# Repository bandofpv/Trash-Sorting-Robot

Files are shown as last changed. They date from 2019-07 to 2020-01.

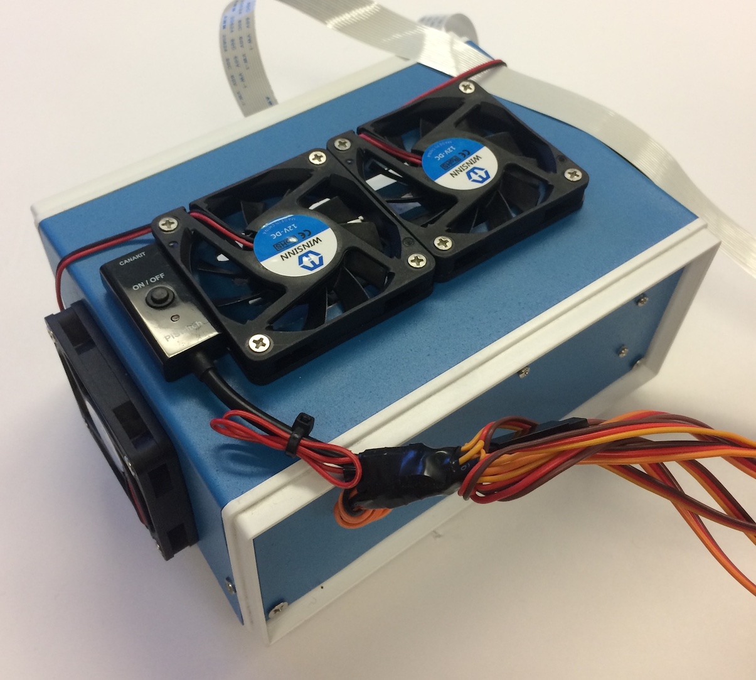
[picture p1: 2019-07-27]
Images/project-box-out.JPG

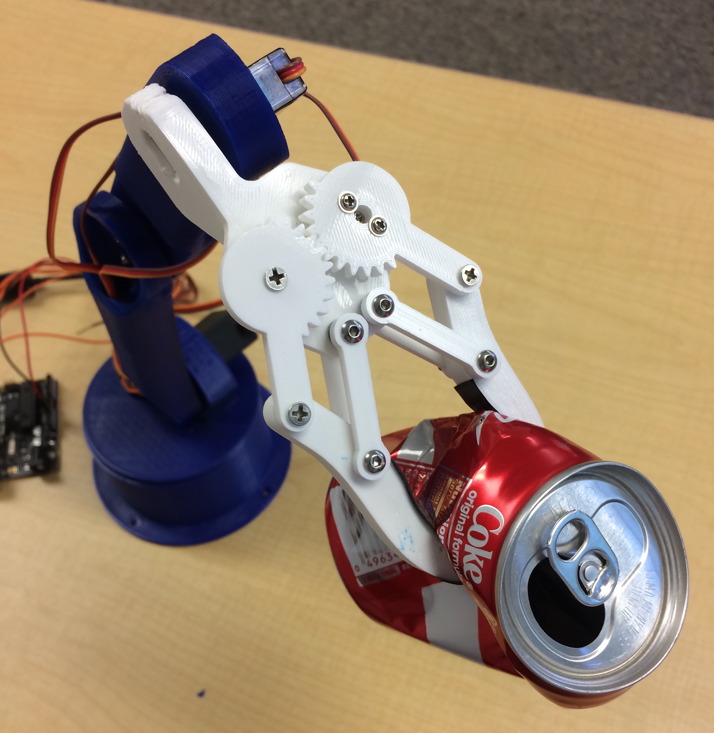
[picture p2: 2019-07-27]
Images/robotic-claw-can.JPG

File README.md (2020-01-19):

# Trash_Sorting_Robot

## Helpful Resources:

* [Recycle Image Set](https://github.com/garythung/trashnet)
* [How to Train Tensorflow Object Detection Model on Windows 10](https://github.com/EdjeElectronics/TensorFlow-Object-Detection-API-Tutorial-Train-Multiple-Objects-Windows-10)
* [How to Train Tensorflow Lite Object Detection Model in Cloud TPUs](https://medium.com/tensorflow/training-and-serving-a-realtime-mobile-object-detector-in-30-minutes-with-cloud-tpus-b78971cf1193)
* [How to Build and Install Tensorflow From Source on Windows 10](https://medium.com/@amsokol.com/how-to-build-and-install-tensorflow-gpu-cpu-for-windows-from-source-code-using-bazel-d047d9342b44)
* [Object Detection with Google Coral USB Accelerator](https://www.pyimagesearch.com/2019/05/13/object-detection-and-image-classification-with-google-coral-usb-accelerator/)
* [USB-to-Serial Communication with Raspberry Pi and Arduino](https://www.sunfounder.com/blog/rpi-ard/)
* [3D Printed Robotic Arm](https://howtomechatronics.com/tutorials/arduino/diy-arduino-robot-arm-with-smartphone-control/)

## Repository Contents:

### [Arduino](https://github.com/bandofpv/Trash_Sorting_Robot/tree/master/Arduino) - files used for Arduino to control robotic arm:
* [basicMovement](https://github.com/bandofpv/Trash_Sorting_Robot/tree/master/Arduino/basicMovement) - .ino file to perform basic movement with robotic arm
* [roboticArm](https://github.com/bandofpv/Trash_Sorting_Robot/tree/master/Arduino/roboticArm) - .ino file to control robotic arm to pick up and drop off a piece of recycling detected from the Raspberry Pi

### [Documentation](https://github.com/bandofpv/Trash_Sorting_Robot/tree/master/Documentation) - files documenting my build process:
* [Bill_of_Materials.pdf](https://github.com/bandofpv/Trash_Sorting_Robot/blob/master/Documentation/Bill_of_Materials.pdf) - .pdf file including all my parts used in my project 
* [Notebook.pdf](https://github.com/bandofpv/Trash_Sorting_Robot/blob/master/Documentation/Notebook.pdf) - .pdf file including my notebook that I used when building my robot

### [Images](https://github.com/bandofpv/Trash_Sorting_Robot/tree/master/Images) - images of my project

### [RPI](https://github.com/bandofpv/Trash_Sorting_Robot/tree/master/RPI) - files used for Raspberry Pi to perform object detection:
* [recycle_ssd_mobilenet_v2_quantized_300x300_coco_2019_01_03](https://github.com/bandofpv/Trash_Sorting_Robot/tree/master/RPI/recycle_ssd_mobilenet_v2_quantized_300x300_coco_2019_01_03) - .tflite and .txt files of the trained recycle model and lables to perform object detection
* [recycle_detection.py](https://github.com/bandofpv/Trash_Sorting_Robot/blob/master/RPI/recycle_detection.py) - python code used to perform object detection and communicate with Arduino

### [Tensorflow](https://github.com/bandofpv/Trash_Sorting_Robot/tree/master/Tensorflow) - files used for training model:
* [CSV](https://github.com/bandofpv/Trash_Sorting_Robot/tree/master/Tensorflow/CSV) - .csv files of both the train and test image set
* [Images](https://github.com/bandofpv/Trash_Sorting_Robot/tree/master/Tensorflow/Images) - .jpg images of recycling materials and .xml files of the annotated images
* [SaveModel](https://github.com/bandofpv/Trash_Sorting_Robot/tree/master/Tensorflow/SaveModel) - frozen graph of trained model
* [TFLite](https://github.com/bandofpv/Trash_Sorting_Robot/tree/master/Tensorflow/TFLite) - .tflite file of trained model and .tflite file of compiled model for Google Coral USB Accelerator
* [TFRecord](https://github.com/bandofpv/Trash_Sorting_Robot/tree/master/Tensorflow/TFRecord) - .record files of both the train and test images set used for training
* [ssd_mobilenet_v2_quantized_300x300_coco_2019_01_03](https://github.com/bandofpv/Trash_Sorting_Robot/tree/master/Tensorflow/ssd_mobilenet_v2_quantized_300x300_coco_2019_01_03) - .config, .ckpt, and .pb files of the quantized model used for transfer learning
* [labelmap.pbtxt](https://github.com/bandofpv/Trash_Sorting_Robot/blob/master/Tensorflow/labelmap.pbtxt) - label map used for training

## Tutorial:

[Hackser.io Tutorial](https://www.hackster.io/bandofpv/recycle-sorting-robot-with-google-coral-b52a92)

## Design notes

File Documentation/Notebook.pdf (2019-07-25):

Important Links:

Waste sorting Medium:
https://towardsdatascience.com/how-to-build-an-image-classifier-for-waste-sorting-6d11d3c9c47 8 (https://towardsdatascience.com/how-to-build-an-image-classifier-for-waste-sorting-6d11d3c9c478)

An Edge TPU Demo Medium:
https://blog.ml6.eu/our-edge-tpu-demo-project-cbc9bea5a355?gi=7440a077a13c

Installing Tensorflow on windows Medium: https://medium.com/@amsokol.com/how-to-build-and-install-tensorflow-gpu-cpu-for-windows-fro m-source-code-using-bazel-d047d9342b44 (https://medium.com/@amsokol.com/how-to-build-and-install-tensorflow-gpu-cpu-for-windows-from-source-code-using-bazel-d047d9342b44)

Training model in 30 minutes Medium: https://medium.com/tensorflow/training-and-serving-a-realtime-mobile-object-detector-in-30-min utes-with-cloud-tpus-b78971cf1193 (https://medium.com/tensorflow/training-and-serving-a-realtime-mobile-object-detector-in-30-minutes-with-cloud-tpus-b78971cf1193)

Object Detection with Edge TPU Pyimagesearch: https://www.pyimagesearch.com/2019/05/13/object-detection-and-image-classification-with-google-coral-usb-accelerator/ (https://www.pyimagesearch.com/2019/05/13/object-detection-and-image-classification-with-google-coral-usb-accelerator/)

EdjeElectronics training model GitHub: https://github.com/EdjeElectronics/TensorFlow-Object-Detection-API-Tutorial-Train-Multiple-Obj ects-Windows-10 (https://github.com/EdjeElectronics/TensorFlow-Object-Detection-API-Tutorial-Train-Multiple-Objects-Windows-10)

Trashnet GitHub: https://github.com/garythung/trashnet

Communication between Raspberry Pi and Arduino via USB-to-Serial: https://www.sunfounder.com/blog/rpi-ard/

3D printed robotic arm:
https://howtomechatronics.com/tutorials/arduino/diy-arduino-robot-arm-with-smartphone-control/

June 10, 2019:

Goals: Get started labeling data & setup RPI.

What I did & learned: I got halfway with labeling my 2.5K+ images for object detection. I made the bordering boxes to big so I had to fix all of them. RIP. I got to boot up my RPI. I got to check my inventory. I learned a little about how to set up my RPI to work with my edge TPU accelerator. I learned that I took an L and deleted my trained model so I have to retrain it again.

I also learned that my laptops GPU is too old and I can’t make use of it in the tensorflow-gpu version. Maybe try to borrow someone else's?

Any code & documentation: Github of labeled images → https://github.com/bandofpv/Trash_Sorting_Robot/tree/61fb91e893919938b6e709a3e1639e927 30c2b46 (https://github.com/bandofpv/Trash_Sorting_Robot/tree/61fb91e893919938b6e709a3e1639e92730c2b46)

I githubbed my model but realized it was the wrong one and realized I deleted the right one. RIP.

Plan for tomorrow: Try to finish labeling images. Setup RPI to work with edge TPU accelerator. Hope I can set up my training environment with tensorflow v1.9.

June 11, 2019:

Goals: Work on labeling. Finish installing TPU stuff.

What I did & learned: I labeled more images. I attempted to ssh to my RPI but was unsuccessful. I tried setting up my edge TPU for the RPI but that was too much work for the day. I also finished setting up my training environment on my laptop.

Any code & documentation: Github of labeled images → https://github.com/bandofpv/Trash_Sorting_Robot/tree/e6b9e248af5a54a2eadbdeffdf42c4b608 3c089b (https://github.com/bandofpv/Trash_Sorting_Robot/tree/e6b9e248af5a54a2eadbdeffdf42c4b6083c089b)

Plan for tomorrow: Try to finish labeling and try to start training.

June 12, 2019:

Goals: Continue labeling. Try to get the real-time object tracking working with the edge TPU accelerator and RPI camera.

What I did & learned: I learned how to use google’s edge TPU classification engine and use the RPI camera to actually classify images as either the 1,000 different objects that are in the
COCO dataset. I also got to use the OpenCV library to get boxes around the object that the pre-trained model recognizes using the classification engine.

Any code & documentation: Github of labeled images → https://github.com/bandofpv/Trash_Sorting_Robot/tree/77f7b33f8d09e02bd1dfe609c44aa23b97 848fdc (https://github.com/bandofpv/Trash_Sorting_Robot/tree/77f7b33f8d09e02bd1dfe609c44aa23b97848fdc)

Plan for tomorrow: Finish labeling images. Try to start training. Maybe start programming Arduino. Work on documentation.

June 13, 2019:

Goals: Finish labeling. Get ready for training → convert XML to CSV to TFRecord.

What I did & learned: I learned how to convert my XML files to CSV and then to TFRecord files. I also learned how to configure the pipeline.config file used to my training. I learned how to delete a docker image and container.

Any code & documentation: Github of labeled images → https://github.com/bandofpv/Trash_Sorting_Robot/tree/8abc70e8a31fdf7ffc08f747d077cbad0e4 5af50 (https://github.com/bandofpv/Trash_Sorting_Robot/tree/8abc70e8a31fdf7ffc08f747d077cbad0e45af50)

Github of training files → https://github.com/bandofpv/train_files/tree/6059fe5c8c78cdadbbaaf28bb0fb8572eddbdcc0

Plan for tomorrow: Start the training and work on my robotic arm.

June 14, 2019:

Goals: Start the training

What I did & learned: I learned how to train my model locally. Realized that it takes forever to train so I’m going to train on the cloud using google's cloud TPUs. I also learned that of all the waste that we produce, 75% is recyclable, yet only 30% is actually recycled. This is because of the contamination rates in the recycling centers. Human sorting adds a huge amount of error in sorting through trash/recycle.

Any code & documentation: Don’t have any code yet because my model is still training. After training in the cloud instead of locally.

Plan for tomorrow: Try to finish up training and start converting it to .tflite and compile it for the edge tpu.

June 17, 2019:

Goals: Learn to control a servo with Arduino and communicate the RPI with the Arduino.

What I did & learned: I learned how to communicate the Arduino using serial. I can make the RPI control the Arduino and the other way around. For my project, I need the RPI to control the Arduino robotic arm. I also learned about inverse kinematics where I can possibly use the robotic arm and move it in a 3D plane based on coordinates. It would be really cool to have the robotic arm move to a certain coordinate based on where the piece of recycling is located at. I also learned how to better use the edge TPU classification functions to identify different objects. I got my code to say if it recognizes a certain object. This is great to recognize where to place the piece of recycling. So if it’s made out of metal, then it would place the object somewhere different then if the object is made of paper.

Any code & documentation: I didn’t have enough time to create a GitHub repository for my code but I will tomorrow.

Plan for tomorrow: Start making my robotic arm hopefully.

Documentation for the first milestone:

Today I completed my first milestone which was to train an object detection model to run on the Coral Edge TPU. In my project, I trained an object detection model to distinguish between different types of recycling.

The first step in completing my first milestone was to install the Coral Edge TPU Python API on to the Raspberry Pi (RPI) in order to use my Coral USB Accelerator. The Coral Accelerator is a TPU or a tensor processing unit that you can connect to any device through a USB (universal serial bus). TPUs are processors designed specifically for machine learning purposes and thus a lot faster and more power efficient when running ML (machine learning) compared to using the RPI’s CPU. That’s why it’s called an accelerator because it accelerates the ML processing. It also includes the word “Edge” meaning all the ML processing is done locally or on the device instead of in the cloud. Using the cloud, you will need good network speed and have to pay a fee in order to use it. Using the cloud for ML is basically using
someone else's powerful TPU, CPU, or GPU to process your ML data and receiving output data via the internet. The benefits of using the Edge TPU is that you don’t need access to the internet making it a lot more versatile option. I still want to sort through recycling even if I don’t have internet access! The Edge TPU is not powerful as the cloud solution but is suitable for my project due to the small amount of data I will be using.

After getting my RPI and Coral USB Accelerator to run a real-time object detection program using a pre-trained model, I immediately noticed how much faster the object detection was. When I tested the same model using only the RPI CPU I observed an average fps (frames per second) of 0.90. With the Coral USB Accelerator, I received an average fps of 10.40. That’s more than 11 times faster! It can process at higher rates.

There is a feature during the installation of the Coral TPU API to run the accelerator at a frequency twice the speed than the default frequency. However, there was a warning that it would get really hot and could cause burns. So I didn’t select this feature due to lack of cooling in my system. This being said, I could easily attach a small fan to cool the USB accelerator and get an fps twice as fast.

The Edge TPU also works best using USB 3 with it’s “host computer” or my RPI. Unfortunately, the RPI 3 Model B+ only has USB 2 capability, not taking full advantage of the Edge TPU’s USB 3. USB 2 transfers data at a slower rate than USB 3. This means if the RPI had USB 3 capability, I can get a faster fps due to the faster rate of data flow. Recently in June, RPI just released the RPI 4 Model B. It not only has a better CPU and RAM but also comes with USB 3 capability. Unfortunately, the Raspbian OS version is built around Python 3.7, making many of the packages I need to use for object detection incompatible. In the near future, everyone will transfer to Python 3.7, making object detection compatible with the RPI 4 Model B. Overall, taking advantage of the Edge TPU’s USB 3.

The next step would be to train my recycling model and compile it to work on the Coral Edge TPU. To explain what a model is, you can simply imagine it as the “brain” of the program. The longer you train the model, the smarter it gets. To train the model, I didn’t start from scratch. I used a technique called transfer learning.

Transfer learning takes a pre-trained model and customizes it to detect certain models. This takes away all the time used to create a custom model and dealing with complicated algorithms. In my case, I used an object detection model from Tensorflow call Mobilenet v2. This model is one of the best pre-trained models out there for ML on low computational powered devices, such as my RPI or smartphones. The Mobilenet v2 runs pretty fast and is decently accurate in terms of classifying the object correctly. There are other models out there that have better accuracy, but in turn, slower to process, resulting in low fps. Using the Mobilenet v2 and transfer learning, I only changed the last few layers in the end to customize my model. Every model has tons of layers each used for a certain purpose, one to recognize each different characteristic of that object. Feeding data or in my case, a video, through those layers, you will get an output of what the model thinks it’s looking at. The image ****** shows how this works. I first need to collect images to create a dataset of pre-annotated images. Luckily, I found a set of images that a pair of students made during their machine learning class at Stanford with 2,500 images of different recyclables.

The set of images were made up of different materials such as paper, cardboard, glass, metal, etc. Using those images, I had to resize them to something smaller to make the training process faster by decreasing the file size. With those images, I had to annotate them. This can be done by an open source application called labelimg to simply draw a box around the object, and type in the name of that object. In my case, I had to draw boxes around pieces of paper, each labeling that it was paper. I had to repeat that for all the images and different recycling materials. After labeling, the labelimg application automatically converts them into .xml files, providing information about where the box is in the image and also the name of the object I specified. In order to train a model, you need to split your data into training and testing sets.

There are many ways to split up your data, such as 50/50, 75/25, 80/20, etc. I chose 80/20 due to the amount and diversity of my data. That means 80% of my images will go into the training set and the other 20% into the testing set. After splitting up the data, I had to convert the .xml files into .csv files so I can later convert that into a TFRecord file.

Converting the .csv files into TFRecord basically assigns a class to each object that you want to detect. In my case, I had 5 classes: cardboard, paper, metal, plastic, and glass. The TFRecord files are also the files that will be used to train my model. Now that I have a train.record and test.record file, I can now move on to creating a label map.

A label map assigns each class number with a name. For example, the first class with id: 1 is assigned the name: cardboard. After creating the label map, I can now move on to configuring the training pipeline. This can be done by changing some parameters in the pipeline.config file that came with the pre-trained model. In the pipeline.config file, I had to specify where the program can find the proper paths for my label map, TFRecord files, and my checkpoint files (comes with the pre-trained model). The checkpoint files act just like a checkpoint would in a video game. It saves progress during training. This being said, I can simply stop training, and resume it at any time. After setting up the pipeline.config file, we can now start training! You can do this in two different ways, locally or in the cloud.

Using the cloud is a lot faster because as I stated earlier, you're basically using someone else’s super expensive computer to do all the training. I attempted this using Google's cloud machine learning platform but faced many errors and I decided to give up on it. So, I just trained the model locally on my laptop. This process is extremely slow and takes tons of time. As I trained the model, the program provides information about its progress and how many training steps it has completed through. Each step signifies the number of times at which the model updates its weights and biases. That is a completely different topic to explain so just think of it as each step makes the model smarter through various distinctions. More distinctions equal smarter model. In my model, I trained it around 13,000 steps. Depending on the model and the number of layers you want to retrain will affect the number of steps needed for training. Using the Mobilenet v2 model, getting a loss average below 2 is a good threshold to end training. That’s exactly what I did. You can see the graph to the ****** showing how the loss or inaccuracy of the model decreases in an exponential decay curve and ending with an average loss below 2. It’s also important to notice that the Coral Edge TPU requires an optimization technique called quantization.

This basically takes all the 32-bit floating-point numbers such as weights to the nearest 8-bit fixed-point numbers. This makes the model a lot smaller and faster without risking a significant loss in accuracy. After training the model, I then had to “freeze” it. That basically means to save the model into a protobuf file. With the .pb file you can use it to run your trained model on any CPU. However, you can’t run that model on the Coral Edge TPU. You have to convert the .pb file into a .tflite file or a tensorflow lite model.

Tensorflow lite is basically a version of Tensorflow, which is the ML library I was using, optimized for mobile usage, perfect for my RPI and the Coral USB Accelerator. In order to convert it into tensorflow lite, I needed to build TF (Tensorflow) from source. This was a lot of work! I found different tutorials about building TF from source on my laptop and kept on getting errors. I finally was able to get TF up and running by making a new Windows account because my username had a space in it, resulting in a path not found errors. I also had to do research on another bug I had with Bazel.

Bazel is a build tool just like make and cmake. TF wasn’t made specifically to use Bazel which lead to many errors. I finally resolved the errors and was able to use TOCO to transfer the frozen graph into a .tflite file. The final step before testing the model would be to compile the .tflite file into a model that can be used on the Coral Edge TPU. Using the Edge TPU Compiler, I compiled my .tflite another .tflite file but now compatible with the Coral USB Accelerator. As seen in the picture on the *****, it states that 99% of the model will be run on the Edge TPU and the other 1% will run on the CPU. This takes a lot of load off of the RPI and focuses all ML processing on the Coral USB Accelerator. This leaves the RPI CPU with only a little ML processing and delivering live video feed onto the desktop. To make the process of retraining an object detection model for the Coral Edge TPU easier to understand, I included a flowchart to demonstrate the process visually.

Now that I’m done with the model, I can finally test it! Using the
edge.tpu.detection.engine I can simply input my re-trained model with the live video feed to get the outputted label, confidence, and bounding box of the object that my model recognizes. This is made super easy thanks to the Edge TPU Python API. With this API, you not only can do object detection but also image classification.

Image classification simply classifies if an image includes certain objects such as a cat or dog, but doesn’t state where the object is. That is the main difference between object detection and image classification. For example, if I had a photo of a cat and used an object detection and image classification model on the same image, the object detection model will tell me that there is a cat in the image as well as where it is located, while image classification model will only tell that there is a cat in the image.

Object detection is more complicated and thus requires more computational power than image classification. In my project, I need to use object detection, so my robotic arm will know where to pick up the object according to where it is located. After using the Python API for object detection, I used the imutils module to display real-time video from the RPI camera onto the actual desktop. I also used imutils to get approximate readings of the average fps to test the efficiency of my model. Finally, I used OpenCV, which is an open source library compatible with Python, used for computer vision programs. In my case, I used it to draw information onto the desktop window. For example, I used it to draw bounding boxes around the objects my model recognizes, the corresponding name of the object, and how confident my model is about recognizing that object. Putting this all together, we can test out my model!

After starting the program I immediately faced a major issue. The model kept thinking that the whole video frame was cardboard. This happens due to two reasons, first, I had more images of cardboard than the other materials, and second, all the images were taken using a white background. Having more images of cardboard makes the model more biased to think the object is cardboard. This issue can be fixed, but I will have to take more photos of the other images to balance the number of images I have per object. For the second issue, taking all the pictures with a white background has its advantages and disadvantages. Its advantage is that it doesn’t require tons of images because all the materials will be trained on the same background, making distinguishing the object from the background easier. The disadvantage is that the model won’t be able to detect objects on a background other than white. This also can be fixed with more images with different backgrounds and lighting. However, with only 2,500 images, it’s good that all my images have the same background due to the small amount of data. The common issue I faced is lack of data.

Usually, models have hundreds of thousands of images for their model. Unfortunately, this takes a lot of time and wouldn’t be possible to complete in the time I have at BlueStamp. After the program, I will continue to add to this model to make it more accurate and more versatile by adding images with different backgrounds and lighting, as well as balancing out the number of images I have for each object. Finally, to minimize errors in my model, I simply tested out the object detection using a white background. Soon enough, it worked! There was one bug in the model that I faced even after using a white background. The model kept thinking a metallic lid was glass, not metal. This is mainly due to my labeling of images that included both metal and glass. A couple of images I used for training were glass jars that also had a metal lid on, so I made two bounding boxes around the metal and glass part of the image. This lead to the confusion of the model because sometimes the metal lid overlapped the glass jar in the image. That’s why the metal lid kept on being recognized as glass. Just like the other bugs in my model, it can be solved simply with more data. Other than that, the model performed really well with detecting different materials at different angles and lighting. I also ended up getting an average fps of 14.50. Better than the pre-trained model! This is due to the number of objects the pre-trained model could recognize compared to my re-trained model. The pre-trained model could detect 91 different objects while my model could only detect 5 different objects. Again, I could get better results if I were to use USB 3, a faster frequency on my Coral USB accelerator, and more data. Finally, I am very satisfied with the results and that I finally got it working.

Now that I’m finished with my first milestone, I will now move onto my second milestone which is to build my robotic arm.

July 1, 2019:

Goals: Start building robotic arm and finish video.

What I did & learned: I started building my robotic arm. I only finished building half of it. Just the arm not the hand. I also finished my first milestone video and documentation that I will add to my website next.

Any code & documentation: Documentation can be found above. No code yet!

Plan for tomorrow: Finish building my robotic arm.

July 2, 2019:

Goals: Finish building my robotic arm.

What I did & learned: I finished building my robotic arm. I also learned that by using a rubber band to help support my arm helps it a lot when picking up objects by taking off the stress from the servo motor. I also learned how to customize my README.md file in GitHub to make it look more organized.

Any code & documentation:
https://github.com/bandofpv/Trash_Sorting_Robot/tree/f8b447600e2c1575d659181dce3dbc261 9c91677 (https://github.com/bandofpv/Trash_Sorting_Robot/tree/f8b447600e2c1575d659181dce3dbc2619c91677)

Plan for tomorrow: Finish soldering components of robotic arm and start programming the arm.

July 3, 2019:

Goals: Finish soldering components of robotic arm and start programming the arm.

What I did & learned: I soldered all the wires together with pins to plug into the arduino. I also put electrical tape and heat shrink around the exposed wires. I learned how to slowly move the arduino to a specific angle. I also created a function for this too.

Any code & documentation: I didn’t setup a GitHub repository yet, but I will!

Plan for tomorrow: Try to finish up programming robotic arm and try to implement inverse kinematics.

Documentation for second milestone:

Today, I finished my second milestone which was to build and program my robotic arm. My robotic arm plays a key part in my project by picking up different recyclables and sorting them depending on it’s material.

The first step in completing this milestone was to get all my 3D printed parts printed and ready. Luckily, I found a predesigned 3D printed arm that I found decently compatible for my application. The 3D printed parts were printed out off a material called PLA (Polylactic Acid). It is very cheap and most well known material for 3D printing. It is also strong enough for my project. After getting all my 3D printed parts, I had to assemble it with my servos.

I used a total of six servos. Three heavy metal geared servos and three 9 gram plastic geared servos. The three metal geared servos will be used to pivot the base of the arm and to move the lower two joints of the arm. The reason why I used metal geared servos for these parts of the arm is because those joints have to support all the weight of the arm and the object it is holding. Metal geared servos are a lot stronger and more robust than plastic geared motors due to the material of the gears. Plastic geared servos also tend to have a lower torque than metal geared servos. The only benefit is that they are much smaller and lighter. I used the 3 plastic geared servos for the top three joints of the arm including the clamping mechanism for this reason.

There were two different versions of the metal geared servo. One with high torque and one with high speed. In my project, I chose the servo with high torque, overall sacrificing the speed at which it rotates. This is done by the gear configuration in the servo. With higher torque, I can carry heavier objects. In order to control the servos of my robotic arm I used an Arduino UNO.

The Arduino UNO is a microcontroller that can be easily programmed on the Arduino IDE. Microcontrollers allow you to receive and transport signals to different peripherals such as sensors and in my project servos. There are three wires that come out of the servo.

One is ground, then 5 volts, and then signal. The 5v and ground wires are just used to power the servo motor while the signal wire is used to connect with the arduino and control the servo. The servo can be controlled using a communication protocol called PWM, Pulse Width Modulation.

Modulation is the act of modifying or changing a frequency. In PWM it changes the width of each pulse in the digital signal. Digital signals can be thought of either on or off. Using PWM, the digital signal consists of pulses, turning on or off but at certain times. In PWM, there is something called duty cycle. Duty cycle is measured in percent of how long each pulse is in the on position. For example a duty cycle of 70% means that the signal is 70% on and 30% off. The image below helps visualize this.

The Arduino can actually send PWM signals thanks to the built-in Servo library. With this library, all you have to do is assign the servo to a pin and set the degree at which you want it to turn to. With it’s pre-built functions, being able to control a servo with the arduino is simple.

Building the robotic arm was a big challenge due to the lack of documentation on building some parts of the arm. I found it extremely difficult to build the clamping mechanism. I wasn’t sure how to construct it because I was only provided with one picture of how it should look like. I was able to use washers for the clamping mechanism joints in order to reduce friction, taking off stress from the servo. Calibrating the clamp for my servo was the next hurdle because I need to make sure that when the servo is turned all the way, the clamp would be fully closed. If I didn’t do this, the clamp would never be able to close.

After building the robotic arm, I had to wire all servos to an external power supply and connect the signal wires to the arduino. All the 5v and ground wires of the servos were all soldered together to a 5 volt 2 amp power supply that connects to a wall outlet. I also used the power supply to power up the arduino too. Using an external power supply, I can provide more current to all the servos than if I were to use the usb port connecting the arduino to the computer. This also allows me to carry heavier objects. Finally, to connect the servo signal pins to the arduino, I had to plug them into PWM capable I/O pins. There is only a selective amount of pins that can be used on the arduino that can output PWM signals. Luckily, there are exactly six PWM pins on the arduino.

After programming the robotic arm to move the servos in specific angles, I was able to pick up different objects and place them behind the robot. One challenge I faced was that the servos would just “snap” into position. Forcing the servo to move very fast into a specific angle while supporting the weight of the arm and the object its holding, putting a lot of stress on the servos that could potentially damage it. To solve this, I created a function called sweep.

Given the servo, the angle it needs to move, and the speed at which you want it to move, I can make the servo move slowly into its desired position. This is done using a for loop and a delay. The for loop will slowly increment the servo angle every few milliseconds specified in the delay function. The delay function will pause the program for a specified amount of time. Putting these together, my sweep function increments the servo angle every 15 ms. This helps the servo move a lot slower, putting less stress on the motor and gears. I’m very pleased I was able to construct my robotic arm and I look forward to moving onto my third milestone.

July 5, 2019:

Goals: Try to finish second milestone

What I did & learned: I finished second milestone schematic and documentation. I also learned that due to the limitations of my servos, the fact that it can only rotate 180 degrees, it isn’t worth it to program inverse kinematics. I can only change the location of the object in the z axis. The x and y axis won’t really be affected do to the limitations of my servo. To program for my z axis change, I found a function in opencv that I can find the angle between the object and were my robotic arm is. This angle can be translated to the angle of my base servo. I can’t wait to finally mount my camera and finish my third milestone.

Any code & documentation: GitHub code for robotic arm: https://github.com/bandofpv/roboarm/tree/a26b0afe9ef835a5a643e566bf98a95bccea0f30

Plan for tomorrow: Try to finish second milestone.

July 8, 2019:

Goals: Finish second milestone.

What I did & learned: Finished second milestone video and website. I also started working on connecting the arduino with rpi. I found a way to simply send bytes from the rpi to the arduino telling the arduino, the distance the object is away from the object, the material (so it knows where to drop off the object, and then the angle at which the robotic arm needs to move in order to pickup the object. I also learned a little about GitHub pages. I think it would be cool to create a tutorial to help others build my project and apply it to the many solutions it can help solve not only by sorting trash.

Any code & documentation: I didn’t commit anything to my GitHub....

Plan for tomorrow: Start programming for third milestone.

July 9, 2019:

Goals: Start third milestone.

What I did & learned: Finished my third milestone! I found out a way to calibrate my camera with my robotic arm. The camera can’t be perfectly aligned with the robotic arm so I had to draw circles of the arm’s range of motion and then align them with the circles on my object detection. It was very finicky and trial and error. I also learned about software licensing. I will use the MIT license for my code so others can use my code for other purposes with ease. I also added a LICENSE file on my GitHub too.

Any code & documentation: GitHub (Still have to comment code but whatever): https://github.com/bandofpv/Trash_Sorting_Robot/tree/c5f7c046fabc5ab3dc46fd07993a8be19d 0c4c66 (https://github.com/bandofpv/Trash_Sorting_Robot/tree/c5f7c046fabc5ab3dc46fd07993a8be19d0c4c66)

Plan for tomorrow: Finish video and documentation for third milestone. Fix any bugs I may face. Start modifications!!!

Introduction to project:
Did you know that the average contamination rate in communities and businesses range up to 25%? That means one out of every four pieces of recycling you throw away doesn’t get recycled. This is caused due to human error in recycling centers. Traditionally, workers will sort through trash into different bins depending on the material. Humans are bound to make errors and end up not sorting the trash properly, leading to contamination. As pollution and climate change become even more significant in today’s society, recycling takes a huge part in protecting our planet. By using robots to sort through trash, contamination rates will decrease drastically, not to mention being cost effective and more sustainable. To solve this, I created a recycle sorting robot that uses machine learning to sort between different recycled materials.

Documentation for third milestone:
Today, I completed my third milestone which was to connect my Raspberry Pi to my Arduino using USB-to-Serial communication so my robotic arm can pick up the recognized piece of recycling and drop it according to its material type.

The first step was to mount my RPI camera to my robotic arm so that it can perform object detection. This was done by simply hot gluing the camera to the bottom of my clamping servo of the robotic arm. When the robotic arm is in its default or home position, the camera will be facing directly below the robotic arm. Below is a picture of my camera mounted on my robotic arm.

Next, I had to connect the Arduino and RPI together via a USB cable in order to perform USB-to-Serial communication. The image below shows how I connected my RPI to my Arduino. I reprogrammed the RPI and Arduino to enable communication between each other. On the Arduino, this can easily be done using the built-in Serial functions, like Serial.begin(). This starts serial communication from the USB. Being able to test the Arduino’s serial communication was made easy due to the Arduino IDE’s serial monitor. You can receive and send data via serial communication. By replicating data signals that would come from the RPI, I was able to quickly debug and program the robotic arm.

To program the robotic arm, I assigned variables to store values coming from the RPI. These included the type of material it detected, it’s distance, and which angle the base servo motor needs to turn. With this information, I simply created functions that essentially take the data from the RPI and pick up the object. I experienced many issues trying to get the robotic arm to pick up an object based on its location. My first attempt was to use something called inverse kinematics.

Inverse kinematics for a robotic arm is a mathematical process of inputting a coordinate in a 3D plane and then calculates angles at which each joint of the robotic arm needs to turn in order to reach that coordinate. I originally found a library for the Arduino that can do inverse kinematics and translate that to angles that each servo needs to turn. Unfortunately, this library was not very good and didn’t include in-depth documentation on how to use the library. I also noticed that the Arduino has very limited processing power, taking forever to get an output after it process through all the mathematical formulas. I wondered if the RPi could run the inverse kinematics instead. I finally decided that this wasn’t worth it due to the lack of computing power of the RPI CPU. If I were to perform inverse kinematic calculations on the RPI, it would eat away at the CPU load. Overall, making my object detection slower and less efficient. Thus, I decided to use a different solution to this problem.

My solution would be to program three presets for each distance increment. Due to the limitations of my servos, only able to go from angle 0 to 180, I was very limited to which areas the robotic arm can pick up an object on the ground. This made the process a little bit easier with my preset solution. These presets would represent three intervals at which distances the robotic arm can pick up an object. With these presets, I can now start programming the RPI.

In terms of serial communication, I was able to use the serial library in python. I was able to start serial communication and begin to transmit and receive data with the Arduino. This process was a bit confusing because when I tested serial communication with the Arduino and RPI with basic code that can allow me to blink an LED from the RPI’s command line, the code worked perfectly. As soon as I added the tensorflow code to the serial communication code, I consistently observed errors. I later noticed that all the serial data I received started with a b’...’ where … is the string received from the Arduino to the RPI. I later found out that I had to use the .decode() method in order to decode the bytestring (b’...’) to a normal string (...). I also had to make sure I converted all my data from the RPI to the Arduino is in UTF-8. After fixing this, I was able to successfully transmit and receive data via USB-to-Serial communication. Now that I can successfully communicate with my Arduino from my RPI, I can move onto finding a way for my robotic arm to pick up the object based off where it’s located in the video feed.

My first step in doing this is to find the center of the detected object. One might think it is already given, but the object detection API only provides the coordinates of the opposite two corners of the bounding box around the object detected. Using some math, I was able to find the center point of the detected object. This is important, so the robotic arm can grab the center part of the object and not the ends and possibly dropping it. With the center coordinate, I now need to calculate the distance and the angle at which the robotic arm needs to move to pick up the object.

To find the distance and the angle, I needed to create a point that is in the video feed to represent the location of the robotic arm. After creating this point, I can use the distance formula and trigonometry to calculate the distance and angle from the object detected and the robotic arm. Using trigonometry, I was only able to calculate an angle less than 90 degrees. I later found a way to convert these angles to degrees from 0 to 180 (angles that the servo can turn) with more math. With the distances, I later had to create conditional statements comparing the calculated distances with the robotic arm presets.

If the calculated distance was closer to a certain preset than the RPI will tell the Arduino what preset the robotic arm needs to move. I then had to create conditional statements for all five types of materials. For example, if plastic is detected for more than 20 frames than the RPI will send the material type, distance, and angle to the robotic arm. The Arduino will later parse that data and store them into variables as stated earlier. With those values, the Arduino will move the robotic arm to pick up and drop off the object. After it is done with the job, the Arduino will later send a string saying “Done Moving” to the RPI to let it know it's ready to detect more recycling materials. This process was as easy as it seems. My biggest issue was calibrating the robotic arm movement with what is displayed on the camera.

The camera wasn’t perfectly attached on the robotic arm and every little tilt of the camera would ruin the alignment. I also had to reprogram my robotic arm presets because I didn’t realize that the camera did not provide a wide enough angle and had a very narrow field of view causing my original presets to pick up something that wasn’t in the video feed. To calibrate the two, I first created three new presets that were in the video feed. I would then trace the circular movements of the robotic arm presets creating three circles. By drawing these circles, I can now align those circles with the video feed. This process was not straightforward because it was all trial and error. You can see an image of the three circles in the video feed below.

After calibrating and fixing any errors, I was able to get a working robot that can successfully recognize, pick up, and drop off an object in the location based on its material.

July 10, 2019:

Goals: Finish third milestone and work on documentation.

What I did & learned: I was able to fix my code to work. I tried cleaning up my code and added comments to make it more understandable. Doing so, I deleted a very important line that makes sure that the calculated distance from the robotic arm to the object is correct. Without realizing I deleted that, I had to go over tons of troubleshooting under a lot of pressure to get it done in time for the video. Luckily, I was finally able to get it working in time and completed my video. I then continued to comment my code and was able to start my modification milestone

Any code & documentation: Still need to update my GitHub. I have the code it just isn’t organized yet.

Plan for tomorrow: Try to finish documentation and work on modification.

July 11, 2019:

Goals: Work on modification.

What I did & learned: I was able to start drilling things holes to mount my RPI, Arduino, and Fans. I also was able to cut ventilation vents for my fan to help cool my electronics. This means, I was able to learn how to use the dremel! That was super cool because it made tons of sparks when you cut the metal. I basically just planned out how I will be able to fit all the electronics in my box today.

Any code & documentation: Nope...

Plan for tomorrow: Screw robotic arm onto base and finish attaching everything. Get the arm to work and try to solder the fans together.

July 12, 2019:

Goals: Try to almost finish my modifications in terms of finishing the box.

What I did & learned: I was able to almost finish my modifications. I finished drilling everything and now I’m just mounting all the parts. The edge TPU was too thick to use the short M2 screws provided in the assortment kit, so I had to find a workaround using some M3 screws that were longer. The box also didn’t come with any screws, so I had to find some short general purpose screws to mount the backplate of the box. I just need to finish a couple more steps, including soldering all the fans, then I’ll be finally done with my project! I also still want to upgrade my software part of the project after demo night too.

Any code & documentation: Still have to update GitHub….

Plan for tomorrow: Finish box modification and start preparing for demo night!

July 15, 2019:

Goals: Finish project box modification!!!

What I did & learned: I was able to finish mounting all my parts onto my project box. I finished soldering all my cooling fans to a simple barrel connector. I continued to do more testing that my project works. I made some small changes to my code so that the robotic arm is more precise. I didn’t have enough time to figures it out but whatever.

Any code & documentation: GitHub: https://github.com/bandofpv/Trash_Sorting_Robot/tree/f1bd2e2b6a8fc6aaca98fcdeb6eee126a3 b61353 (https://github.com/bandofpv/Trash_Sorting_Robot/tree/f1bd2e2b6a8fc6aaca98fcdeb6eee126a3b61353)

Plan for tomorrow: Get ready for Demo Night

July 16, 2019:

Goals: Get ready for Demo Night

What I did & learned: I basically just worked on my script and timing of everything. My project works pretty well.

Any code & documentation: No code...

Plan for tomorrow: Be fully prepared for Demo Night!!!

July 17, 2019:

Goals: Be completely ready for Demo Night

What I did & learned: I was able to get ready for Demo Night. Constantly preparing my speech.

Any code & documentation: No Code...

Plan for tomorrow: Finish website and final milestone video maybe...

July 18, 2019:

Goals: Work on modifications!

What I did & learned: I was able to finish with some modifications. I was able to add more circle presets for my robotic arm to make it more precise and not miss objects. Asher recommended me to make it go faster, but I unfortunately had bad results. The robot kept missing the objects by a little and the camera wouldn’t be aligned properly. This is caused by the cheap servos. The servo motor doesn’t have much torque and tends to skip gears or not able to get very precise angles when moving fast. I will continue to make it move slow and want to try to pick up objects based on the size and material of the object detected. Right now, it just clamps the hand all the way, which strains the servo and makes it get pretty hot. If I can use a little math, I can calculate the size of the object and be able to pick up the object without damaging the servo motor. I hope I get the time!!! Now that I think about it… That idea isn’t actually possible because the object detection draws bounding boxes around the object. If the object is diagonal, than the box will be massive. Not representing the size of the object properly. I would have to use semantic image segmentation witch can actually draw an outline around the detected object. This would be better for finding the overall size and width of the object. Semantic image segmentation is super complicated though and isn’t supported on the coral edge tpu. This is because the Coral only supports quantized models and being so complex, image segmentation hasn’t been quantized yet. Hopefully in the future!!!

Any code & documentation: GitHub: https://github.com/bandofpv/Trash_Sorting_Robot/tree/3baae28ca106896610c991f2a0db1456d b664373 (https://github.com/bandofpv/Trash_Sorting_Robot/tree/3baae28ca106896610c991f2a0db1456db664373)

Plan for tomorrow: Finish website and final milestone video!!!

Documentation for final milestone:

Today I completed my final milestone which was to mount all the components into a project box, enable the Edge TPU’s maximum frequency, and to make the robotic arm more accurate.

I decided to use an aluminum project box that had sufficient space to fit the Arduino, Raspberry Pi, and the Coral Edge TPU USB Accelerator. Aluminum is great because it acts like a huge heat sink for my components. In order to mount all the hardware in the project box, I used brass standoffs to better help cool the components. The RPI and TPU would reach extremely high temperatures.

These components process the object detection and thus are under a lot of computation load. When the RPI operated outside of the case, it still achieved high temperature levels. I decided to add four fans for active cooling to complement passive cooling from the heat sinks.

Now, I have passive and active cooling to help cool all my components. The four fans all run on 12 volts, so I had to add an extra power supply and solder all the fan wires into a bullet connector for my power supply. With the fans on the RPI did not run hot when running object detection. Usually, it reached high enough temperatures to burn your skin to the touch. With the fans, it ran casually warm. Below is a picture of all my components inside the aluminum project box.

After mounting all the components in a project box with fans, I was also able to reach the maximum frequency the Coral Edge TPU can operate at. When installing the edgetpu API, there is a feature to enable the setting to make the TPU run at a higher frequency than default. This will allow for better frames per second than if running the TPU at a lower frequency. Using this feature, I get one more frame faster than before. I achieved an average of 15.5 fps which is better than my previous 14.5 fps using the default frequency. I also was able to make my robotic arm more accurate.

This was done by adding more distance presets. As explained during my Third Milestone, I used distance presets to pick up the detected object based on how far it was from my robotic arm. By adding more, it would become even more precise and accurate. Below is an image showing more preset circles from the video feed.

I would still like to add more modifications to my project. For example, I’m thinking of adding a relay switch to automatically turn on and off the cooling fans based on how hot the CPU was. If the CPU passes a certain temperature, the RPI will send a signal to the relay to switch the cooling fans on. This would prevent wearing out the cooling fans because they will only turn on when needed.

Finally, I’m super excited I successfully completed my project in a short period of time.

Reflection:

My experience at Bluestamp was fantastic. I always loved to build things at home. Bluestamp is an environment filled with students and instructors that share my passion for building and learning new things specifically in engineering. This was a super unique experience that I would not be able to experience at my high school.

July 19, 2019:

Goals: Finish up everything!!!

What I did & learned: I was able to complete my final milestone video and finish up ally the documentation. I finished my website too, just need to add my videos that need to be uploaded.

Any code & documentation: GitHub: https://github.com/bandofpv/Trash_Sorting_Robot

Plan for tomorrow: Nothing…

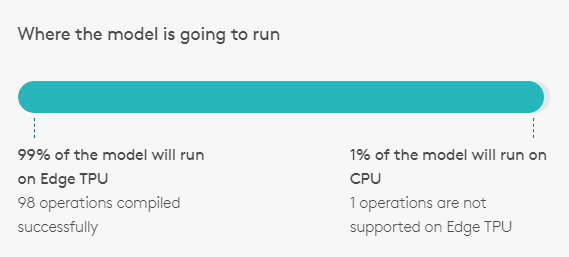
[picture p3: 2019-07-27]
Images/edgetpu.png

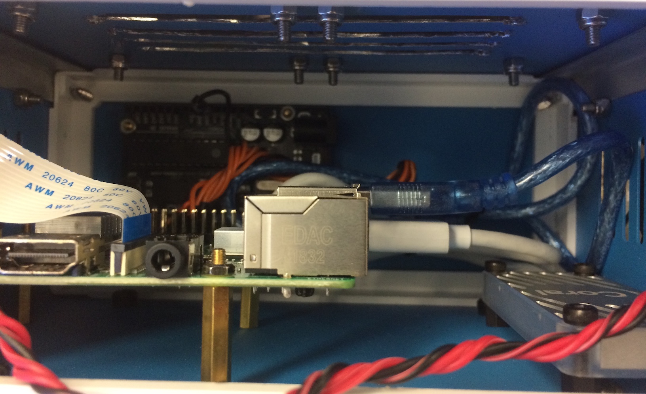
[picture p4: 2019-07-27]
Images/project-box-in.JPG

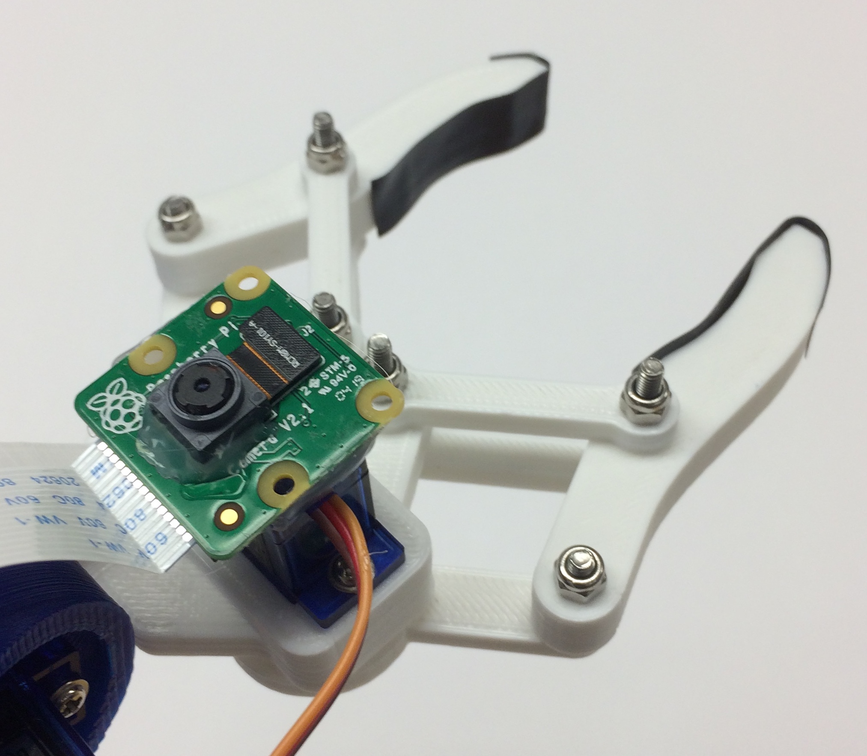
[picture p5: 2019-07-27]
Images/robotic-claw.JPG

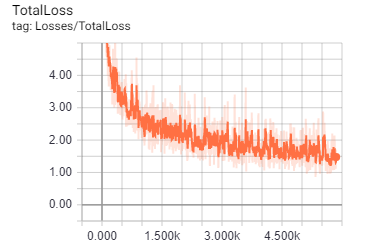
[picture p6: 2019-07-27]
Images/loss.png

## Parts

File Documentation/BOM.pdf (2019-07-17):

# BlueStamp Engineering Student Bill of Materials (BOM)

Please fill this out for all parts that will be required for your project. If you cannot find information, move on and ask your instructor when emailing this to them. Item # Description Vendor Part Number Qty Cost Link to Where to Purchase

1 3D Parts | N/A | N/A | 1 N/A | https://howtomechatronics.com/tutorials/arduino/diy-arduino-robot-arm-with-smartphone-control/ 2 Arduino Uno R3 | Amazon | B008GRTSV6 | 1 | $17.90 https://www.amazon.com/Arduino-A000066-ARDUINO-UNO-R3/dp/B008GRTSV6
3 5V 2A DC Power Supply | Amazon | B00GUO5WUI | 1 | $7.99 https://www.amazon.com/iMBAPrice-Adapter-Listed-Supply-5-Feet/dp/B00GUO5WUI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 4 SG90 Servos | Amazon | B07F2XDZZ7 | 1 | $20 https://www.amazon.com/dp/B07F2XDZZ7/ref=psdc_2234131011_t1_B0716V3WNH?th=1
5 M3 Lock Nuts | Amazon | B075ZZW7VL | 1 | $8 https://www.amazon.com/100Pcs-Stainless-Self-Lock-Inserted-Clinching/dp/B075ZZW7VL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
6 M3x20 Screws | GetFPV | 2872 | 1 | $6.99 https://www.getfpv.com/m3x20-button-head-titanium-screws-10pcs.html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
7 MG996R Servos | Amazon | B07F7YZW7Q | 1 | $23 https://www.amazon.com/dp/B07F7YZW7Q/ref=psdc_2234131011_t1_B0716V3WNH?th=1
8 Samsung 32GB Micro SD Card | Amazon | B06XWN9Q99 | 1 | $8 https://www.amazon.com/Samsung-MicroSD-Adapter-MB-ME32GA-AM/dp/B06XWN9Q99/ref=dp_ob_title_ce
9 RPI Camera | Amazon | B01ER2SKFS | 1 | $29 https://www.amazon.com/Raspberry-Pi-Camera-Module-Megapixel/dp/B01ER2SKFS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
10 RPI Canakit | Amazon | B07BC7BMHY | 1 | $54.99 https://www.amazon.com/CanaKit-Raspberry-Premium-Clear-Supply/dp/B07BC7BMHY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
11 Google Coral USB Accelerator | Sparkfun | DEV-15317 | 1 | $74.95 https://www.sparkfun.com/products/15317
12 | Adafruit Flex Cable for Raspberry Pi Camera - 1 meter | Amazon | B01BQUSQNU | 1 | $6.98 | https://www.amazon.com/Adafruit-Flex-Cable-Raspberry-Camera/dp/B01BQUSQNU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
13 | M2 Male Female Brass Spacer Standoff Screw Nut Assortment Kit Amazon | B01N1IUTVT | 1 | $9.99 https://www.amazon.com/HVAZI-270pcs-Female-Standoff-Assortment/dp/B01N1IUTVT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
14 | uxcell 6.69" x 5.12" x 2.95" | Amazon | B07BFBQFT6 | 1 | $34.39 https://www.amazon.com/dp/B07BFBQFT6/ref=psdc_495308_t2_B07G95V7YC?th=1#customerReviews 15 | LoveRPi Performance Heatsink Set | Amazon | B018BGRDVS | 1 | $4.99 https://www.amazon.com/LoveRPi-Performance-Heatsink-Raspberry-Heatsinks/dp/B018BGRDVS
16 | 60mm Fan 12V DC Brushless Quiet Cooling | Amazon | B07GX86CJN | 1 | $10 https://www.amazon.com/dp/B07GX86CJN/ref=twister_B07P3BLGNM?_encoding=UTF8&psc=1
17 | 12volt Power Supply | Amazon | B00FEOB4EI | 1 | $13.49 https://www.amazon.com/R-Tech-UL-Listed-Switching-Supply-Adapter/dp/B00FEOB4EI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

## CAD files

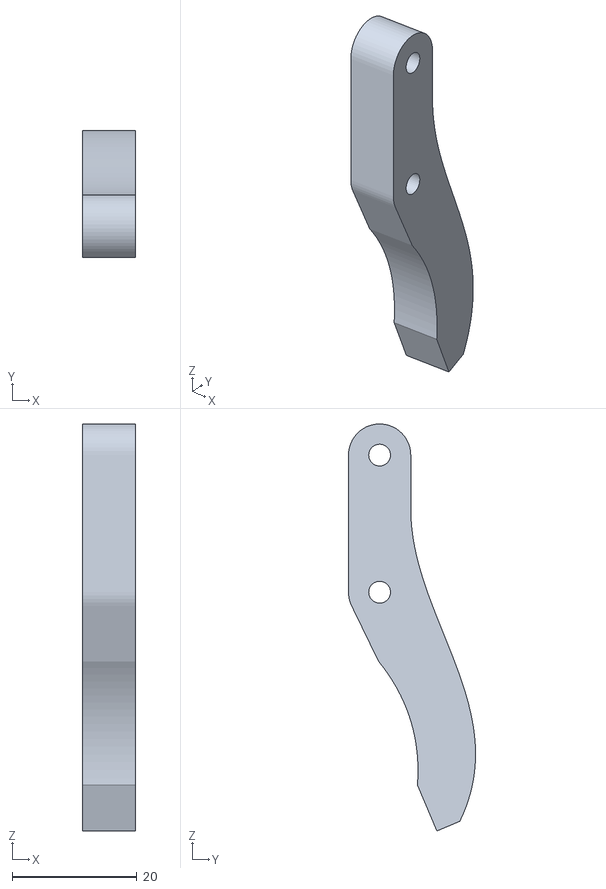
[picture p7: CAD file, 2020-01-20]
3D/gripper.STL
8.50 x 20.4 x 65.3

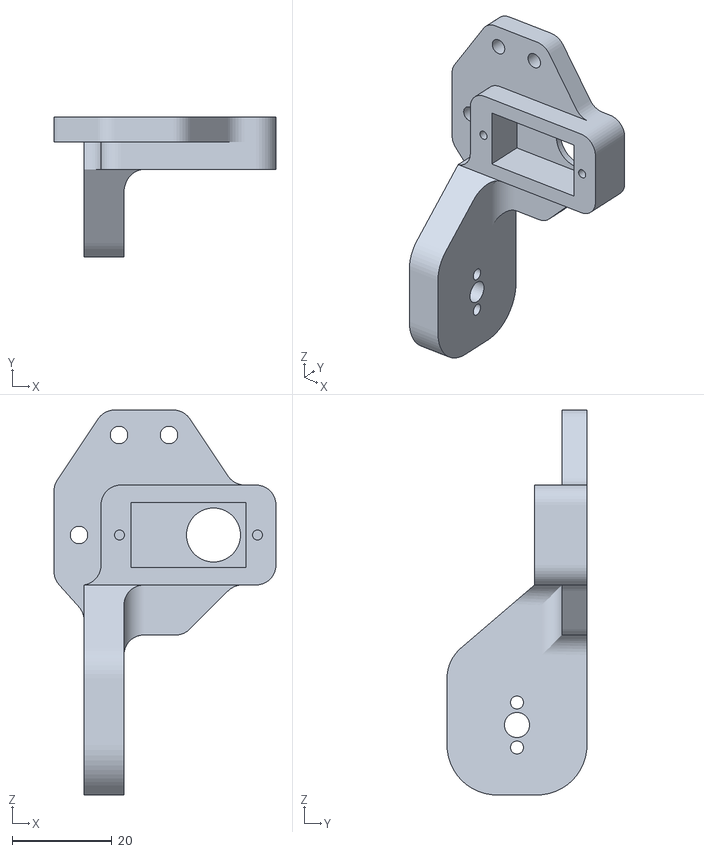
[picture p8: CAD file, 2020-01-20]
3D/gripper_base.STL
44.4 x 28.0 x 77.0

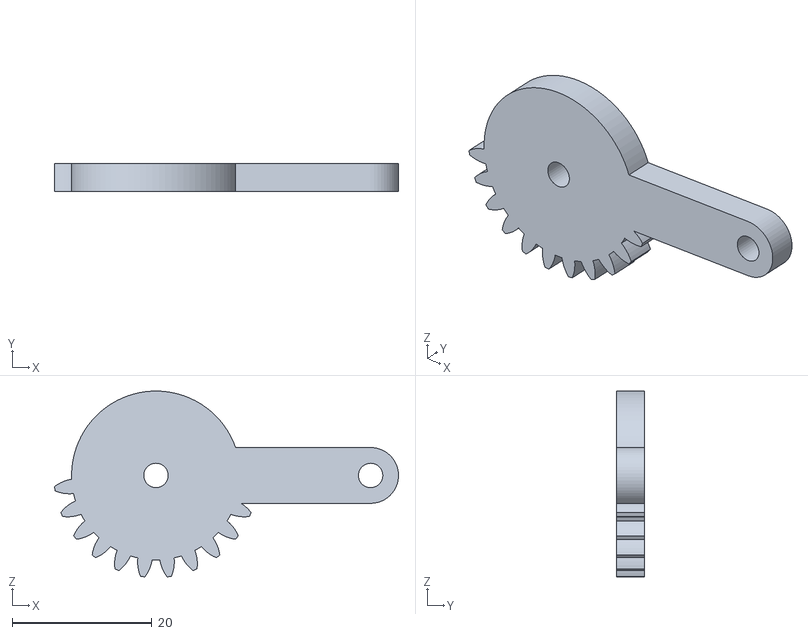
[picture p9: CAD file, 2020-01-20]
3D/gear_01.STL
49.3 x 4.00 x 26.6

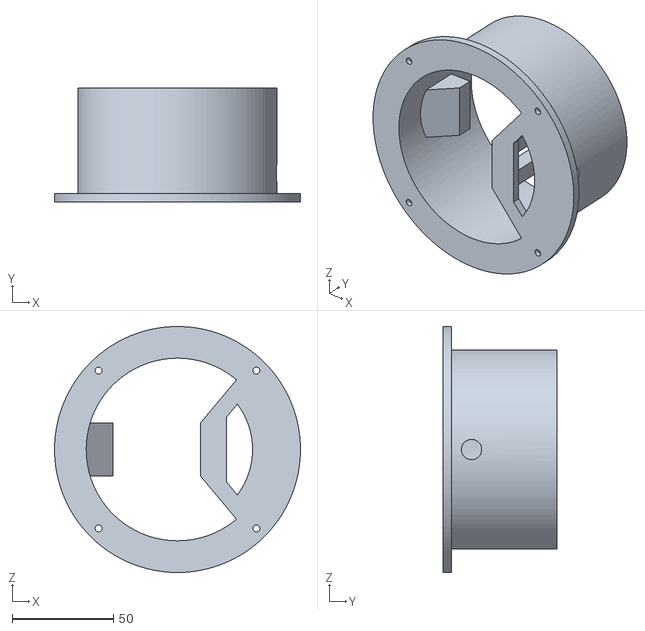
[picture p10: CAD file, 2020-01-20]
3D/base.STL
121.2 x 56.0 x 121.2

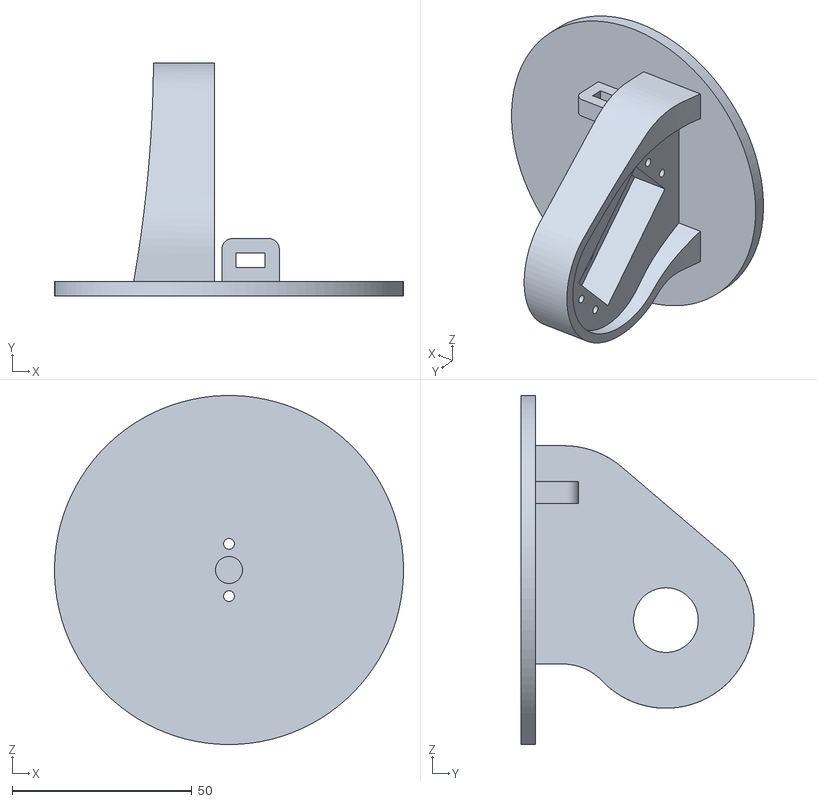
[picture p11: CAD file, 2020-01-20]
3D/waist.STL
97.0 x 64.8 x 97.0

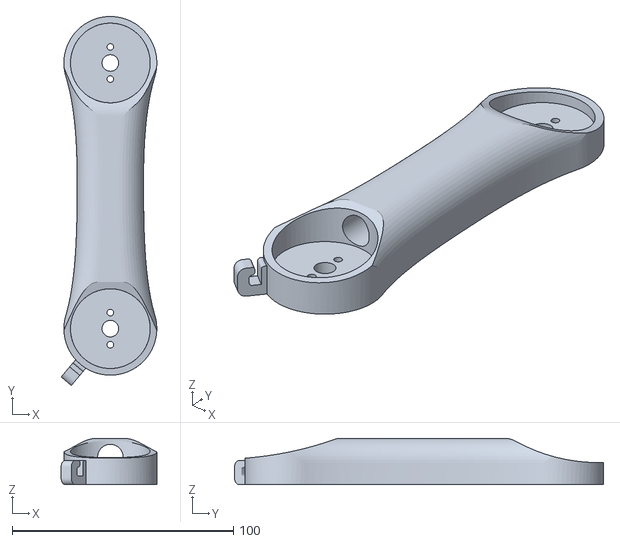
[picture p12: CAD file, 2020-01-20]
3D/arm_01.STL
43.2 x 166.7 x 21.0

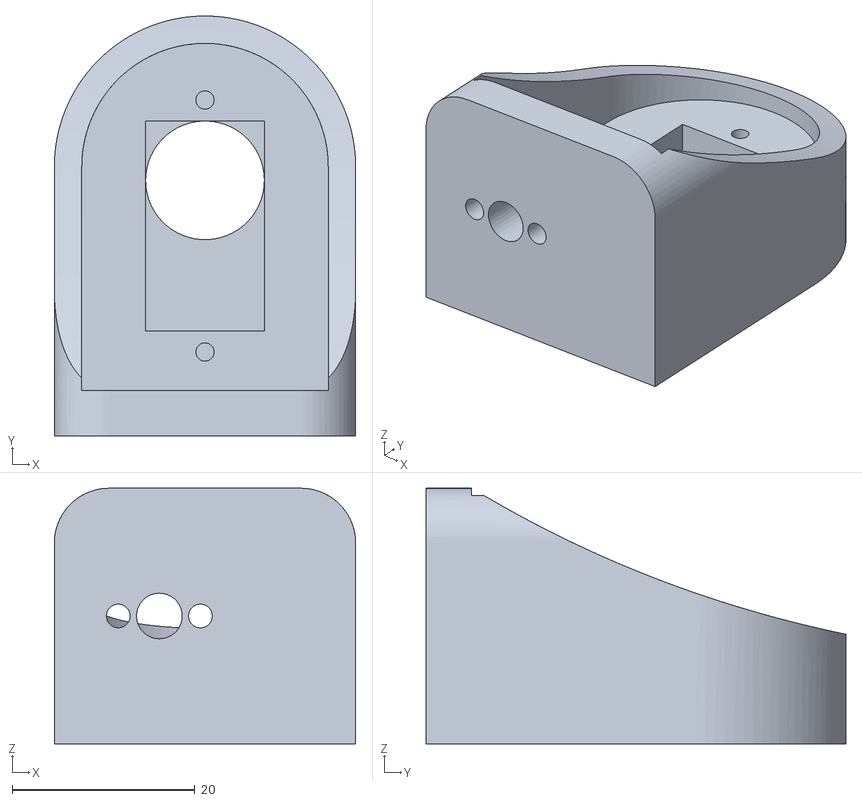
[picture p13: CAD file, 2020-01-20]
3D/arm_03.STL
33.0 x 46.0 x 28.0

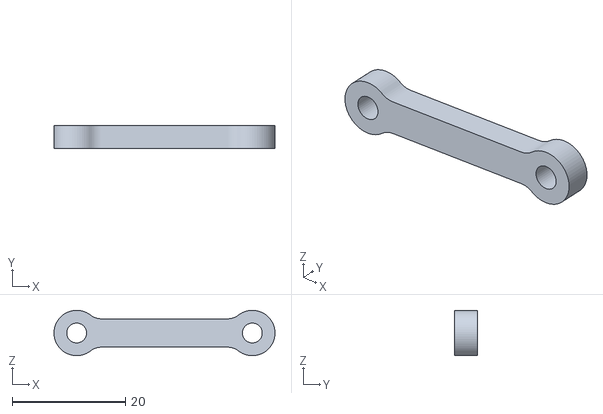
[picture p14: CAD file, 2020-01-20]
3D/grip_link.STL
39.0 x 4.00 x 8.00

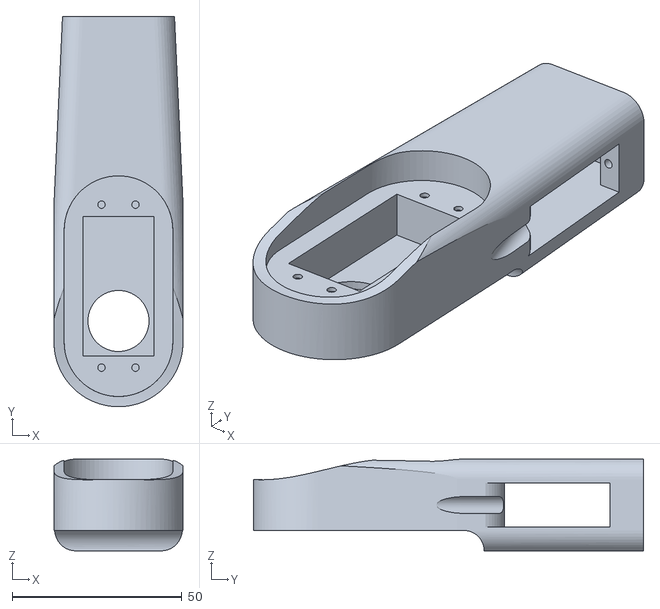
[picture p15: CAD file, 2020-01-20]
3D/arm_02.STL
38.0 x 115.0 x 27.0

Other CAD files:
3D/gear_02.STL

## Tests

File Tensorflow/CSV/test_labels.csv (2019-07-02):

filename | width | height | class | xmin | ymin | xmax | ymax
cardboard323.jpg | 512 | 384 | cardboard | 1 | 1 | 512 | 384
cardboard324.jpg | 512 | 384 | cardboard | 1 | 1 | 512 | 384
cardboard325.jpg | 512 | 384 | cardboard | 1 | 1 | 512 | 384
cardboard326.jpg | 512 | 384 | cardboard | 1 | 1 | 512 | 384
cardboard327.jpg | 512 | 384 | cardboard | 68 | 1 | 512 | 384
cardboard328.jpg | 512 | 384 | cardboard | 1 | 1 | 512 | 384
cardboard329.jpg | 512 | 384 | cardboard | 1 | 1 | 512 | 384
cardboard330.jpg | 512 | 384 | cardboard | 1 | 1 | 512 | 384
cardboard331.jpg | 512 | 384 | cardboard | 1 | 1 | 478 | 384
cardboard332.jpg | 512 | 384 | cardboard | 1 | 1 | 512 | 384
cardboard333.jpg | 512 | 384 | cardboard | 1 | 60 | 455 | 384
cardboard334.jpg | 512 | 384 | cardboard | 1 | 1 | 512 | 384
cardboard335.jpg | 512 | 384 | cardboard | 1 | 1 | 512 | 384
cardboard336.jpg | 512 | 384 | cardboard | 1 | 1 | 512 | 384
cardboard337.jpg | 512 | 384 | cardboard | 1 | 1 | 512 | 384
cardboard338.jpg | 512 | 384 | cardboard | 1 | 1 | 512 | 384
cardboard339.jpg | 512 | 384 | cardboard | 1 | 1 | 512 | 384
cardboard340.jpg | 512 | 384 | cardboard | 1 | 1 | 512 | 384
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

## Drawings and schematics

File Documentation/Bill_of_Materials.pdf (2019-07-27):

# Bill of Materials (BOM)

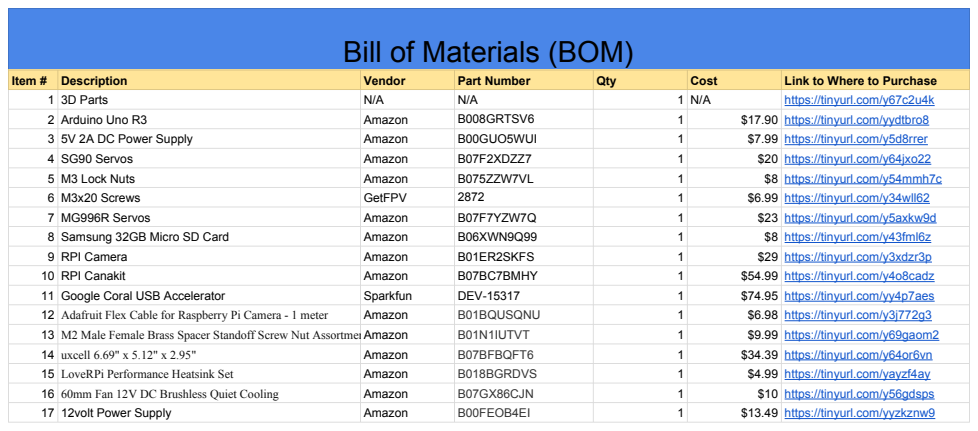
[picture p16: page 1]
Item #; Description; Vendor; Part Number; Qty; Cost; Link to Where to Purchase; 1 3D Parts; https://tinyurl.com/y67c2u4k; 2 Arduino Uno R3; Amazon; B008GRTSV6; $17.90 https://tinyurl.com/yydtbro8; 3 5V 2A DC Power Supply; B00GUO5WUI; $7.99 https://tinyurl.com/y5d8rrer; 4 SG90 Servos; B07F2XDZZ7; $20 https://tinyurl.com/y64jxo22; 5 M3 Lock Nuts; B075ZZW7VL; $8 https://tinyurl.com/y54mmh7c; 6 M3x20 Screws; GetFPV; $6.99 https://tinyurl.com/y34wll62; 7 MG996R Servos; B07F7YZW7Q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

12volt Power Supply Amazon | B00FEOB4EI | 1 $13.49 https://tinyurl.com/yyzkznw9

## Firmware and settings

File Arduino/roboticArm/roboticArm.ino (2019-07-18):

/*
   This code is used to control the robotic arm based on the inputs from the
   Raspberry Pi. The Raspberry Pi will detect the recycle and will tell the Arduino
   to move the robotic arm in the location the object is detected at. Based on
   the material, the robotic arm will place the object in the correct loaction.
*/

// add Servo library
#include <Servo.h>

// create variables to store data from RPI
int numBlink = 0;
int distance = 0;
int material = 0;
int angle = 90;

// create variables to store servo posistions
int shoulderPos = 90;
int elbowPos = 90;
int wrist1Pos = 90;
int wrist2Pos = 90;
int handPos = 90;
int basePos = 90;

// create Servo objects to control servos
Servo shoulder;
Servo elbow;
Servo wrist1;
Servo wrist2;
Servo hand;
Servo base;

// create flash function (will flash Arduino LED by the number you input)
void flash(int n) {
  for (int i = 0; i < n; i++) {
    digitalWrite(13, HIGH);
    delay(500);
    digitalWrite(13, LOW);
    delay(500);
  }
}

void setup() {
  // begin serial communication with RPI and send default string to RPI to confirm connection
  Serial.begin(9600);
  Serial.println("Connected to Arduino");

  // assign Arduino LED to pin 13
  pinMode(13, OUTPUT);

  // attach servo objects to correct pin number
  shoulder.attach(11);
  elbow.attach(10);
  wrist1.attach(9);
  wrist2.attach(6);
  hand.attach(5);
  base.attach(3);

  // move arm to home position to face camera down
  homeState();
}

void loop() {
  // send default string to RPI to confirm connection
  Serial.println("Connected to Arduino");

  // if the RPI sends a signal to Arduino
  if (Serial.available()) {
    // change values of variables to what the RPI sends
    numBlink = Serial.parseInt();
    material = Serial.parseInt();
    distance = Serial.parseInt();
    angle = Serial.parseInt();

    // flash LED and move the arm to pick and drop the object based on its material
    flash(numBlink);
    pickUp();
    dropOff();

    // go back to home state
    homeState();

    // send string to let RPI know that the arm is done moving
    Serial.println("Done Moving");
    Serial.flush();
  }
  delay(1000);
}

/*
   sweep function to make servos move slowly!

   input the servo object, the current servo angle, the angle you
   want the servo to move to, and the speed at which you want to turn
   the servo. Bigger number ==> slower speed. Smaller number ==> faster speed.
*/
void sweep(Servo servo, int oldPos, int newPos, int servoSpeed) {
  if (oldPos <= newPos) {
    for (oldPos; oldPos <= newPos; oldPos += 1) {
      servo.write(oldPos);
      delay(servoSpeed);
    }
  }

  else if (oldPos >= newPos) {
    for (oldPos; oldPos >= newPos; oldPos -= 1) {
      servo.write(oldPos);
      delay(servoSpeed);
    }
  }
}

// pickUp function that will move robotic arm to specified distance and angle sent from RPI
void pickUp() {  
  // if the object detected is closest to the small/closest circle distance preset
  if (distance == 1) {
    sweep(base, basePos, angle, 30);
    basePos = angle;
    sweep(hand, handPos, 160, 30);
    handPos = 160;
    sweep(wrist2, wrist2Pos, 35, 30);
    wrist2Pos = 35;
    sweep(elbow, elbowPos, 180, 30);
    elbowPos = 180;
    sweep(shoulder, shoulderPos, 65, 30);
    shoulderPos = 65;
    sweep(hand, handPos, 45, 30);
    handPos = 45;
    distance = 0;
  }

  // if the object detected is between the smallest and medium circle distance preset
  else if (distance == 2) {   
    sweep(base, basePos, angle, 30);
    basePos = angle;
    sweep(hand, handPos, 160, 30);
    handPos = 160;
    sweep(wrist2, wrist2Pos, 37, 30);
    wrist2Pos = 37;
    sweep(elbow, elbowPos, 175, 30);
    elbowPos = 175;
    sweep(shoulder, shoulderPos, 60, 30);
    shoulderPos = 60;
    sweep(hand, handPos, 45, 30);
    handPos = 45;
    distance = 0;
  }

  // if the object detected is closest to the medium circle distance preset
  else if (distance == 3) {
    sweep(base, basePos, angle, 30);
    basePos = angle;
    sweep(hand, handPos, 160, 30);
    handPos = 160;
    sweep(wrist2, wrist2Pos, 32, 30);
    wrist2Pos = 32;
    sweep(elbow, elbowPos, 165, 30);
    elbowPos = 165;
    sweep(shoulder, shoulderPos, 55, 30);
    shoulderPos = 55;
    sweep(hand, handPos, 45, 30);
    handPos = 45;
    distance = 0;
  }

  // if the object detected is between the medium and big circle distance preset
  else if (distance == 4) {
    sweep(base, basePos, angle, 30);
    basePos = angle;
    sweep(hand, handPos, 160, 30);
    handPos = 160;
    sweep(wrist2, wrist2Pos, 32, 30);
    wrist2Pos = 32;
    sweep(elbow, elbowPos, 160, 30);
    elbowPos = 160;
    sweep(shoulder, shoulderPos, 50, 30);
    shoulderPos = 50;
    sweep(hand, handPos, 45, 30);
    handPos = 45;
    distance = 0;
  }

  // if the object detected is closest to the big/farthest circle distance preset
  else if (distance == 5) {
    sweep(base, basePos, angle, 30);
    basePos = angle;
    sweep(hand, handPos, 160, 30);
    handPos = 160;
    sweep(wrist2, wrist2Pos, 32, 30);
    wrist2Pos = 32;
    sweep(elbow, elbowPos, 150, 30);
    elbowPos = 150;
    sweep(shoulder, shoulderPos, 45, 30);
    shoulderPos = 45;
    sweep(hand, handPos, 45, 30);
    handPos = 45;
    distance = 0;
  }
}

// dropOff function that will drop off the object to a location based off its material
void dropOff() {
  // if the material detected was cardboard
  if (material == 1) {
    sweep(shoulder, shoulderPos, 90, 30);
    shoulderPos = 90;
    sweep(elbow, elbowPos, 0, 30);
    elbowPos = 0;
    sweep(wrist2, wrist2Pos, 90, 30);
    wrist2Pos = 90;
    sweep(base, basePos, 0, 30);
    basePos = 0;
    sweep(hand, handPos, 160, 30);
    handPos = 160;
    material = 0;
  }

  // if the material detected was glass
  else if (material == 2) {
    sweep(shoulder, shoulderPos, 90, 30);
    shoulderPos = 90;
    sweep(elbow, elbowPos, 0, 30);
    elbowPos = 0;
    sweep(wrist2, wrist2Pos, 90, 30);
    wrist2Pos = 90;
    sweep(base, basePos, 45, 30);
    basePos = 45;
    sweep(hand, handPos, 160, 30);
    handPos = 160;
    material = 0;
  }

  // if the material detected was metal
  else if (material == 3) {
    sweep(shoulder, shoulderPos, 90, 30);
    shoulderPos = 90;
    sweep(elbow, elbowPos, 0, 30);
    elbowPos = 0;
    sweep(wrist2, wrist2Pos, 90, 30);
    wrist2Pos = 90;
    sweep(base, basePos, 90, 30);
    basePos = 90;
    sweep(hand, handPos, 160, 30);
    handPos = 160;
    material = 0;
  }

  // if the material detected was paper
  else if (material == 4) {
    sweep(shoulder, shoulderPos, 90, 30);
    shoulderPos = 90;
    sweep(elbow, elbowPos, 0, 30);
    elbowPos = 0;
    sweep(wrist2, wrist2Pos, 90, 30);
    wrist2Pos = 90;
    sweep(base, basePos, 135, 30);
    basePos = 135;
    sweep(hand, handPos, 160, 30);
    handPos = 160;
    material = 0;
  }

  // if the material detected was plastic
  else if (material == 5) {
    sweep(shoulder, shoulderPos, 90, 30);
    shoulderPos = 90;
    sweep(elbow, elbowPos, 0, 30);
    elbowPos = 0;
    sweep(wrist2, wrist2Pos, 90, 30);
    wrist2Pos = 90;
    sweep(base, basePos, 180, 30);
    basePos = 180;
    sweep(hand, handPos, 160, 30);
    handPos = 160;
    material = 0;
  }
}

// homeState function that will hold the camera facing down to perform obejct detection
void homeState() {
  sweep(base, basePos, 90, 30);
  basePos = 90;
  sweep(wrist2, wrist2Pos, 60, 30);
  wrist2Pos = 60;
  sweep(elbow, elbowPos, 110, 30);
  elbowPos = 110;
  sweep(shoulder, shoulderPos, 65, 30);
  shoulderPos = 65;
  sweep(hand, handPos, 90, 30);
  handPos = 90;
}

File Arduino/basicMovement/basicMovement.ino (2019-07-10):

/*
 * Basic code that will move robotic arm to preset location,
 * pick up an object, and drop it off behind the arm.
 * 
 * Uses my sweep function that will slow the rate at which 
 * the servo rotates.
 */

// include Servo Library
#include <Servo.h>

// create Servo objects to control servos
Servo shoulder;
Servo elbow;
Servo wrist1;
Servo wrist2;
Servo hand;
Servo base;

void setup() {
  // attach each servo object to a pin number
  shoulder.attach(11);
  elbow.attach(10);
  wrist1.attach(9);
  wrist2.attach(6);
  hand.attach(5);
  base.attach(3);

  // set servos to pickup opbject
   sweep(hand, 90, 160, 30);  
   sweep(wrist2, 90, 160, 30);
   sweep(elbow, 90, 160, 30);
   sweep(shoulder, 90, 15, 30);
   sweep(hand, 160, 0, 30);

  // set servos to drop object
  sweep(shoulder, 15, 90, 30);
  sweep(elbow, 160, 0, 30);
  sweep(wrist2, 160, 90, 30);
  sweep(hand, 0, 160, 30);
}

void loop() {
  // nothing here!
}

/*
 * sweep function to make servos move slowly!
 * 
 * input the servo object, the current servo angle, the angle you 
 * want the servo to move to, and the speed at which you want to turn 
 * the servo. Bigger number ==> slower speed. Smaller number ==> faster speed.
 */
 
void sweep(Servo servo,int oldPos, int newPos, int servoSpeed){
  // if you want the servo to move clockwise
  if (oldPos <= newPos){
    // increase the servo angle by one every servoSpeed ms
    for (oldPos; oldPos <= newPos; oldPos += 1){
      servo.write(oldPos);
      delay(servoSpeed);
   }
  }

  // if you want the servo to move counter-clockwise
  else if (oldPos >= newPos){
    // decrease the servo angle by one every servoSpeed ms
    for (oldPos; oldPos >= newPos; oldPos -= 1){
      servo.write(oldPos);
      delay(servoSpeed);
    }
  }
}

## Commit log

2019-07-02 Added Tensorflow Model Files
    [test_labels.csv, train_labels.csv]
2019-07-02 Added Tensorflow Files to Tensorflow Directory
    [test_labels.csv, train_labels.csv]
2019-07-11 added Arduino code for robotic arm
2019-07-15 Added BOM
    [BlueStamp Bill of Materials (BOM) 2019.xlsx]
2019-07-17 Added BOM to Documentation
2019-07-18 Updated BOM
2019-07-18 Updated name of BOM
2019-07-18 Updated robotic arm code
2019-07-27 edited Bill of Materials
2020-01-20 added 3D files
    [arm_01.STL, arm_02.STL, arm_03.STL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]
